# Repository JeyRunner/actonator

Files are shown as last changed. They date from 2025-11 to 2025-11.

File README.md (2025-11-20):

## Actonator - 3D Printable Robot Actuator


3D printable robot actuator with belt-driven gearbox and custom FOC driver board for the used BLDC motor.
It uses the [CAN SOT Protocol](https://github.com/JeyRunner/can-sot-protocol) for the communication, which allows to not only send commands and receive state changes but also to set configuration parameters dynamically during runtime.

### Features

- Driver board
  - Input: 10 - 24V
  - Output: can drive up to two BLDC motors, each output up to 10A
  - CAN bus communication
  - Encoders connected via two I2C connections
      - Alternatively via two SPI inputs
    - 12 bit encoders
- Gearbox
  - Fully 3d printable
  - 2 stage timing belt based reduction
  - Simple screw-based belt tensioning mechanism
  - ~1:20 reduction
  - Easily back drivable

### Project Structure
- `motor_driver/firmware`: C++ firmware code for the stm32 microcontroller
- `motor_driver/can_client_lib`: Contains the can bus communication protocol definition and host applications to configure and interface with the motor driver.
    - `motorControllerCanProtocol.def.yaml`: Contains the protocol definition.
- `motor_driver/hardware`: Kicad files with schematics for the board and PCB.
- `motor_driver/hardware/output`: Schematics, board layout and manufacturing files.
- `gearbox`: 3D printing stl files for the gearbox.

### Driver Board Electronics
This board is a dual channel brushless motor driver.
The design of the board can be found in the `hardware` subfolder.
In `hardware/output` are all generated files for all versions.

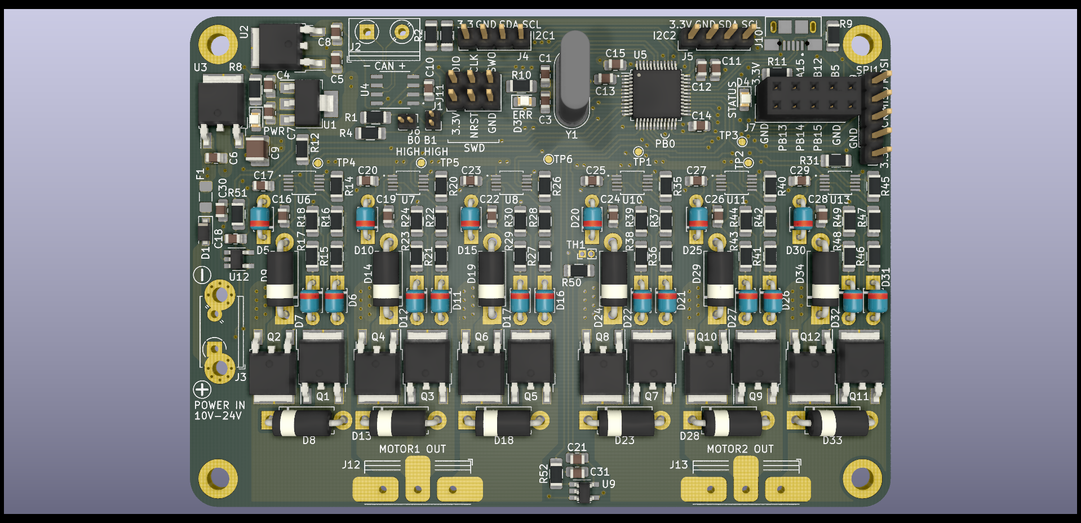
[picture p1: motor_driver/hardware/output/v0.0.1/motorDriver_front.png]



For the full schematic, see [hardware/motorDriver/output/v0.0.1/schematic.pdf](motor_driver/hardware/output/v0.0.1/schematic.pdf).

### Gearbox
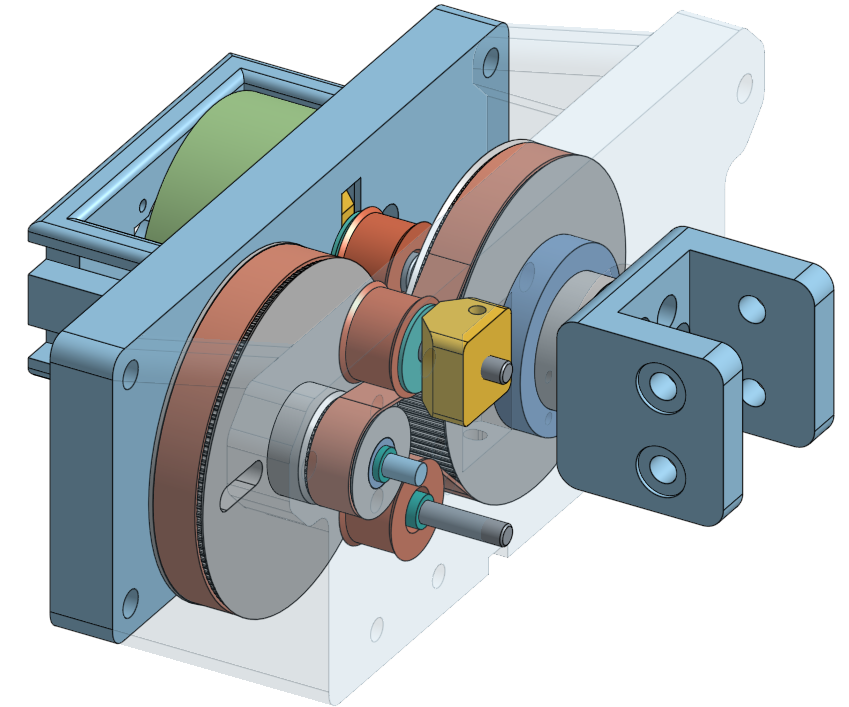
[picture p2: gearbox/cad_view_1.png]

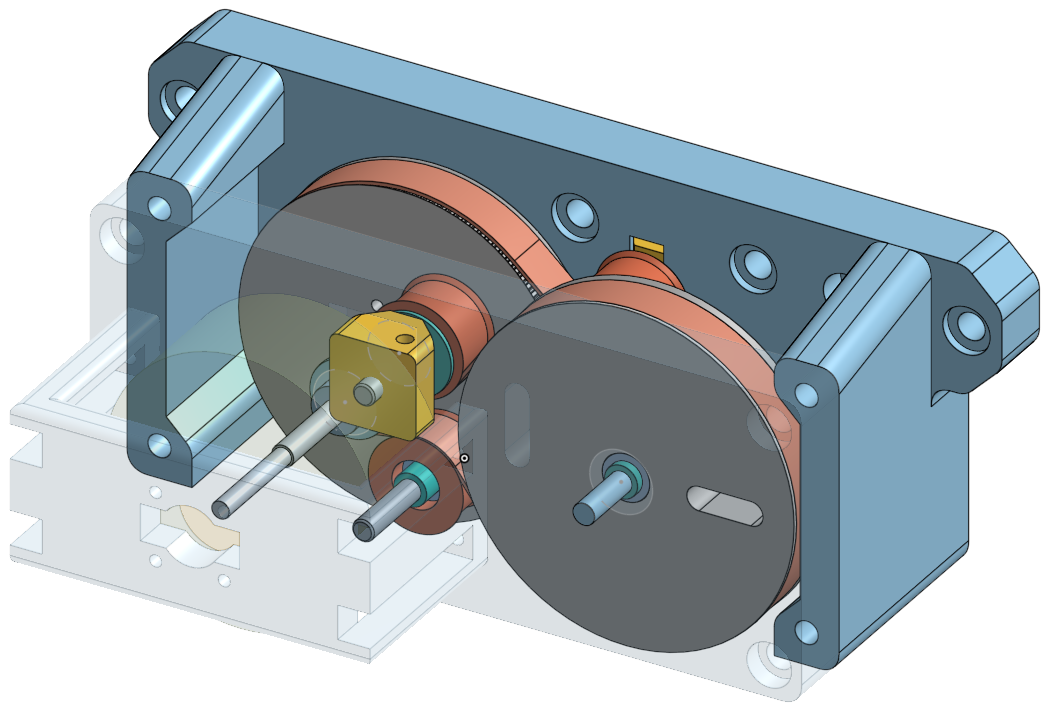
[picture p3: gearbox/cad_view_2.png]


### Usage
First look at [motor_driver/can_client_lib/README.md](motor_driver/can_client_lib/README.md) to compile the communication lib and host control application.
Then compile and flash the microcontroller firmware, see [motor_driver/firmware/README.md](motor_driver/firmware/README.md).

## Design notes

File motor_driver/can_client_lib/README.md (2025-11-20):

# MotorDriver Can Client Library
Interface with the MotorDriver from linux via the can bus. 
Here also the can protocol is defined.

## Usage
First connect a usb-to-CAN adapter of your choice to the computer and setup the can interface:
```bash
sudo ip link set can0 up type can bitrate 500000

# check interface
sudo ifconfig

# test send something
cansend can0 123#42ff4545
```

For `canable` adapters there is a helper script for this in `tools/setup_slcand_can.sh`.

### Configure the Board and Move the Motor
You can configure the motor driver with the `configuration_tool`:
```bash
# in the build folder
# set gains:
./configuration_tool --can-interface can0 --client-id 1 --set-gain-p 1.0 --set-gain-d 0.05
```

Move the actuator in a sinusodial motion:
```bash
# here we also can update the gains:
./example_app -i can0 --client-id 1 \
  --loop-delay-ms 2 `--pd-sin-lambda 0.4` \
  --throttle-limit 0.9 --pd-sin-amplitude 10000 \
  --gain-p -1.5 --gain-d -0.00 
```

## Compile
### Compile the example and configuration execuables
```bash
# install deps
apt-get install libasio-dev libboost-coroutine-dev libboost-dev

mkdir build
cd build
cmake ..
make genCanSotHeaders   # gen protocol headers first
make example_app 
make configuration_tool 
```

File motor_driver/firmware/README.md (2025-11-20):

## Firmware for the Motor Driver Board
Implements field oriented control.

### Structure
```bash
└── src
    ├── canSot           # can protocol (contains autogenerated code)
    ├── cubeMxGenerated  # auto generated code
    ├── motordriver      # main implementation of the bldc motor driver
    └── stm32_custom     # stm specific hardware interface implementation
```

### Compile and Flash Firmware
Note that you first have to generate the can protocol code, see [can_client_lib/README.md](../can_client_lib/README.md) (here run `genCanSotHeaders`). The compile the firmware:
```
mkdir build
cd build
cmake ..
make
```
This will produce the binary `motorDriver_stm32.elf`.

Now you can program the micorcontroller with a programmer that is conneced to the host computer:
```bash
# in the firmware/ folder
openocd -f stm32F103_Debug_self_start.cfg \
	-c "program motorDriver_stm32.elf verify reset exit"
```

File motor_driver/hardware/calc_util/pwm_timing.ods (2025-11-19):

MOSFET |  | Fall Time | Min Pulse Time | Cicle duration (8Bit Res) | Max Freq (8bit Res)
 | @ 5V | 2,00E-05 | 2E-05 | 0,0051 | 196,078431372549
 | @ 10V

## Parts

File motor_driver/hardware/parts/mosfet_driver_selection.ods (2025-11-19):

Name | Functions | Cost for 1 Unit | Link
DRV8305N | - 3 Gait Drivers for the 3 Phases (3 or 6 PWM) - 3 Current Sense Amps for all 3 Phases | ~ 5 EUR | https://www.lcsc.com/product-detail/Motor-Driver-ICs_Texas-Instruments-DRV8305NQPHPRQ1_C701780.html

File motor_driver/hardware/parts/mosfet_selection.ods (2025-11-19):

Calculation Formulas: |  | MOSFET |  |  |  |  |  | 10A |  | 20A |  | 30A
 |  |  | Pack | Vmax GateSource | Q Total (nC) | RDS(ON) | °C/Watt | Power (W) | Temp °C (Room = 20°C) | Power | Temp (Room = 20°C) | Power | Temp (Room = 20°C) | Cost (10 pieces, €)
Power: | RDS(ON) * (Current2) | IRFZ44N (Current) | tht |  | 63 | 0.0175 | 62 | 1.75 | 128.5 | 7 | 454 | 15.75 | 996.5
 |  | AP120N03K | smd big |  | 34 | 0.006 | 62.5 | 0.6 | 57.5 | 2.4 | 170 | 5.4 | 357.5 | 0.98
 |  | SE30100B | smd small |  | 70 | 0.004 | 75 | 0.4 | 50 | 1.6 | 140 | 3.6 | 290
 |  |  |  |  |  |  |  | 0 | 20 | 0 | 20 | 0 | 20
 |  | VSD004N03MS | smd big |  | 85 | 0.004 | 50 | 0.4 | 40 | 1.6 | 100 | 3.6 | 200 | 1.48 | https://www.lcsc.com/product-detail/MOSFETs_Vanguard-VSD004N03MS_C427022.html
 |  |  |  |  |  |  |  | 0 | 20 | 0 | 20 | 0 | 20
 |  | LNG03R031 | smd big |  | 146 | 0.0031 | 68 | 0.31 | 41.08 | 1.24 | 104.32 | 2.79 | 209.72 | 1.98 | https://www.lcsc.com/product-detail/MOSFETs_LONTEN-LNG03R031_C779904.html
 |  |  |  |  |  |  |  | 0 | 20 | 0 | 20 | 0 | 20
 |  | FHP100N03C | tht |  | 26 | 0.0048 | 62.5 | 0.48 | 50 | 1.92 | 140 | 4.32 | 290 | 1.87
 |  |  |  |  |  |  |  | 0 | 20 | 0 | 20 | 0 | 20
 |  |  |  |  |  |  |  | 0 | 20 | 0 | 20 | 0 | 20
 |  | HUAYI HYG030N03LQ1D | smd big |  |  | 0.003 | 110 | 0.3 | 53 | 1.2 | 152 | 2.7 | 317
 |  | TTD120N03AT | smd big |  | 89 | 0.0034 | 60 | 0.34 | 40.4 | 1.36 | 101.6 | 3.06 | 203.6 | 1.52 | https://www.lcsc.com/product-detail/MOSFETs_WUXI-UNIGROUP-MICRO-TTD120N03AT_C691675.html
 |  | HSU150N03 | smd big |  | 39 | 0.0032 | 62 | 0.32 | 39.84 | 1.28 | 99.36 | 2.88 | 198.56 | 2.27 | https://www.lcsc.com/product-detail/MOSFETs_HUASHUO-HSU150N03_C845614.html
 |  | YJG150N03A | smd small |  |  |  |  | 0 | 20 | 0 | 20 | 0 | 20
 |  |  |  |  |  |  |  | 0 | 20 | 0 | 20 | 0 | 20
 |  |  |  |  |  |  |  | 0 | 20 | 0 | 20 | 0 | 20
 |  | No avail | smd small |  | 41 | 0.0018 | 235 | 0.18 | 62.3 | 0.72 | 189.2 | 1.62 | 400.7
 |  |  |  |  |  |  |  | 0 | 20 | 0 | 20 | 0 | 20
 |  |  |  |  |  |  |  | 0 | 20 | 0 | 20 | 0 | 20
 |  | SiR150DP | smd small | 45 V | 32 | 0.0028 | 62.5 | 0.28 | 37.5 | 1.12 | 90 | 2.52 | 177.5 | 9.2 | https://www.mouser.de/ProductDetail/Vishay-Siliconix/SIR150DP-T1-RE3?qs=BJlw7L4Cy78ko2ZoY53%252BgQ%3D%3D
 |  | TPH2R306NH1 | smd small |  |  | 0.0023 | 156 | 0.23 | 55.88 | 0.92 | 163.52 | 2.07 | 342.92
 |  |  |  |  |  |  |  | 0 | 20 | 0 | 20 | 0 | 20
 |  | NTMFS5C430NL | smd small | 40 V | 82 | 0.0014 | 50 | 0.14 | 27 | 0.56 | 48 | 1.26 | 83 | 8 | https://www.lcsc.com/product-detail/MOSFETs_onsemi-NTMFS5C430NLT1G_C194661.html
 |  | From old Multiplex ESC NTMFS4833N | smd small | 30V | 58 | 0.002 | 117 | 0.2 | 43.4
 |  | Driver Current = 1.2A |  |  | T = Q / I

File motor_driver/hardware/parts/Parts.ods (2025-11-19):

Part(s) Type | Values | Parts Per Value | Package/ Dimensions | Required | Voltage | Notes | Picture | Cost With Shipping | Url
Resistor SMD Kit | 0 ohm, 1 Ohm, 2,2 Ohm, 3,3 Ohm, 4,7 Ohm, 5,1 Ohm, 10 ohm, 15 Ohm, 22 Ohm, 33 Ohm, 47 Ohm, 51 Ohm, 62 ohm, 82 Ohm, 100 Ohm, 120 Ohm, 150 Ohm, 180 Ohm, 200 ohm, 220 Ohm, 240 Ohm, 270 Ohm, 300 Ohm, 330 Ohm, 470 ohm, 510 Ohm, 560 Ohm, 680 Ohm, 820 Ohm, 1K Ohm, 1,2 K Ohm, 1,5 K Ohm, 1,8 K Ohm, 2K Ohm, 2,2 K Ohm, 3K Ohm, 3,3 K Ohm, 4,7 K Ohm, 5,1 K Ohm, 5,6 K Ohm, 7,5 K Ohm, 10K Ohm, 12K Ohm, 15K Ohm, 18K Ohm, 20K Ohm, 22K Ohm, 33K Ohm, 43K Ohm, 47K Ohm, 51K Ohm, 75K Ohm, 100K Ohm, 200K Ohm, 300K Ohm, 390K Ohm, 470K Ohm, 680K Ohm, 1M Ohm, 10M Ohm | 20 | Package Code: Imperial: 1206 Metric: 3216 | yes |  | ¼ Watt |  | 7.61 | https://de.aliexpress.com/item/1005003021538603.html?spm=a2g0s.8937460.0.0.38652e0eIeFj74
0805 SMD Ceramic Capacitor Kit |  | 25 | Package Code: Imperial: 0805 | yes |  |  |  | 8.79 | https://www.aliexpress.com/item/592923241.html?pdp_ext_f=%7B%22sku_id%22%3A%2257665256609%22%7D
SMD 0805 LED | Red Green Blue Yellow White | 20 | Package Code: Imperial: 0805 | yes |  |  |  | 2.88 | https://www.ebay.de/itm/373436218990?hash=item56f2887e6e:g:Zz8AAOSwRF1gCoNk
STM32F103C8T6 |  | 1 |  | yes |  |  |  | 9.24 | https://de.aliexpress.com/item/1005002502652952.html
CAN Driver TJA1050 |  | 5 | sop-8 |  |  |  |  | 7.16 | https://de.aliexpress.com/item/1005001716591215.html
UF4007 Ultra Fast Diode |  | 100 | tht |  |  |  |  | 2.64 | https://de.aliexpress.com/item/32854878050.html?pdp_ext_f=%7B%22sku_id%22%3A%2265279246474%22%7D
AMS1117 Spannung Regler Kit | 1,2 V 1,5 V 1,8 V 2,5 V 3,3 V 5V | 10 | smd | OPTIONAL | Vin max = 12V |  |  | 5.06 | https://de.aliexpress.com/item/4000931454820.html
LM2937-3,3 Spannungs Regler 3.3V 500mA |  | 10 | smd | OPTIONAL [selected] | Vin max = 26V Vin min = 5V |  |  | 4.08 | https://de.aliexpress.com/item/1005002503564346.html
UA78M33CDCYR Spannungs Regler 3.3V 500mA |  | 10 | smd | OPTIONAL | Vin max = 25V |  |  | 6.69 | https://de.aliexpress.com/item/1005002054754217.html
L78M05CDT Spannungs Regler 5V 500mA |  | 10 | smd | OPTIONAL | Vin max = 35V Vin min = 7V |  |  | 2.66 | https://de.aliexpress.com/item/32493217336.html
L78xx Spannungs Kit | Adjustable 5V 6V 8V 9V 10V 12V 15V 18V 24V LM317T L7805 L7806 L7808 L7809 L7810 L7812 L7815 L7818 L7824 | 10 | THT | OPTIONAL [selected] | [For Vout = 5V] Vin max = 35V Vin min = 7V |  |  | 7.72
Fuse | 0.5A | 10 | smd | OPTIONAL |  |  |  | 2.00 | https://www.aliexpress.com/item/32901034711.html?pdp_ext_f=%7B%22sku_id%22%3A%2266684643036%22%7D
 |  |  |  |  |  |  |  | SUM:
 |  |  |  |  |  |  |  | 28.52 €
LCSC PARTS
Part(s) Type | Values | Parts Per Value | Package/ Dimensions | Required | Voltage | Notes | Picture | Cost | Url
UF4007 Ultra Fast Diode |  | 100 | tht | yes |  |  |  | 1.34 | https://www.lcsc.com/product-detail/Diodes-Fast-Recovery-Rectifiers_SUNMATE-Elec-UF4007_C424496.html
CAN Driver TJA1050 |  | 5 | sop-8 | yes |  |  |  | 5.05 | https://www.lcsc.com/product-detail/CAN-ICs_NXP-Semicon-TJA1050T-CM-118_C6952.html
LM2937-3,3 Spannungs Regler 3.3V 500mA |  | 2 | smd | yes | Vin max = 26V Vin min = 5V |  |  | 0.78 | https://www.lcsc.com/product-detail/Linear-Voltage-Regulators-LDO_UTC-Unisonic-Tech-LM2937L-33-TQ2-R_C87307.html
UA78M33CDCYR Spannungs Regler 3.3V 500mA |  | 2 | SMD | yes | Vin max = 25V Vin min = 5V |  |  | 0.89
L78M05CDT Spannungs Regler 5V 500mA |  | 10 | smd | yes | Vin max = 35V Vin min = 7V |  |  | 1.14 | https://www.lcsc.com/product-detail/Linear-Voltage-Regulators-LDO_STMicroelectronics-L78M05CDT-TR_C55509.html
KIA78D09F-RTF/P Spannungs Regler 9V 1A |  | 5 | SMD | yes | Vin max = 35V Vin min = 9.5V |  |  | 0.80 € | https://www.lcsc.com/product-detail/Linear-Voltage-Regulators-LDO_KEC-Semicon-KIA78D09F-RTF-P_C69764.html
GRM32ER61C476KE15L Ceramic Capacitor 47uF 16V |  | 5 | smd | yes |  |  |  | 0.83 | https://www.lcsc.com/product-detail/Multilayer-Ceramic-Capacitors-MLCC-SMD-SMT_Murata-Electronics-GRM32ER61C476KE15L_C77101.html
Fuse 30A 24V |  | 5 | smd | yes |  | Breaking Capacity: 150A |  | 0.5 | https://www.lcsc.com/product-detail/Fuses_Shenzhen-JDT-Fuse-JFC1206-2300FS_C136359.html
Fuse 500mA 63V |  | 10 | smd | yes |  |  |  | 0.6
Micro USB B Connector |  | 20 | smd | yes |  |  |  | 0.44 | https://www.lcsc.com/product-detail/USB-Connectors_XKB-Connectivity-U254-051T-4BH83-F1S_C397452.html
Screw terminaL 3 PIN |  | 10 | tht | yes |  |  |  | 0.93 | https://www.lcsc.com/product-detail/Screw-terminal_Ningbo-Kangnex-Elec-WJ126V-5-0-3P_C8401.html
Screw terminaL 2 PIN |  | 5 |  |  |  |  |  | 0.31
LM5106MMX |  | 6 | smd | yes |  |  |  | 7.24
MOSFETS LNG03R031 |  |  |  | yes |  |  |  | 2.38
 |  |  |  |  |  |  | -- SHIPPING | 4.77
 |  |  |  |  |  |  |  | SUM:
 |  |  |  |  |  |  |  | 27.22 €

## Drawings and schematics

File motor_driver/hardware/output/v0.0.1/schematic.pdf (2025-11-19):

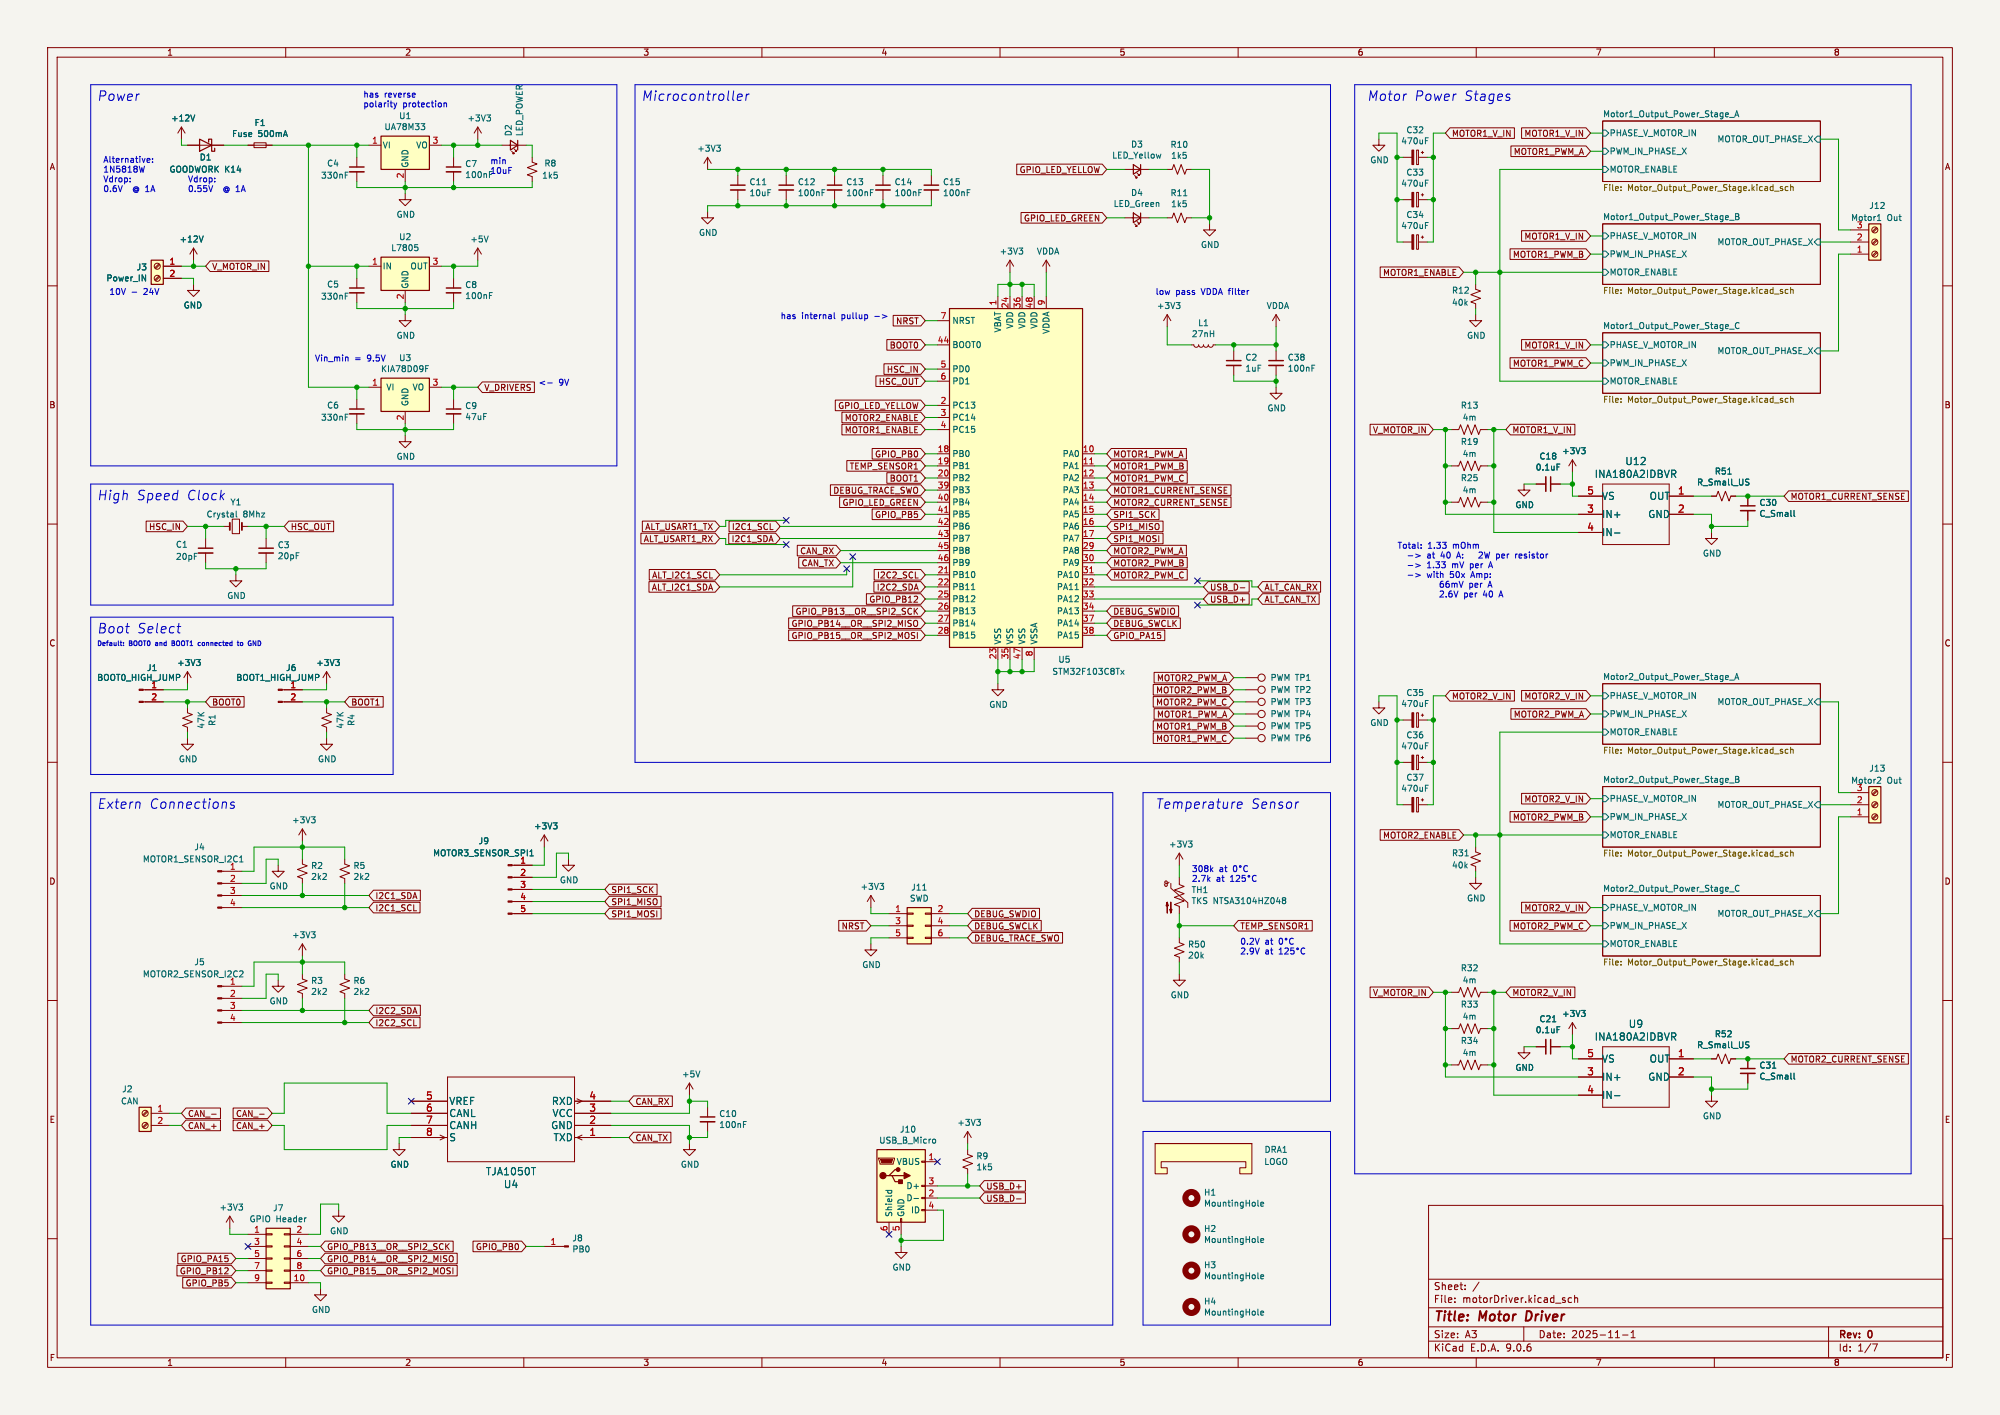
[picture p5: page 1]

2 VO 3 U1 UA78M33 GND GND GND

low pass VDDA filter

1 VSS 23 VDD 24 VSS 35 VDD 36 VSS 47 VDD 48 VSSA

Id: 1/7 Title: Motor Driver File: motorDriver.kicad_sch Sheet: /

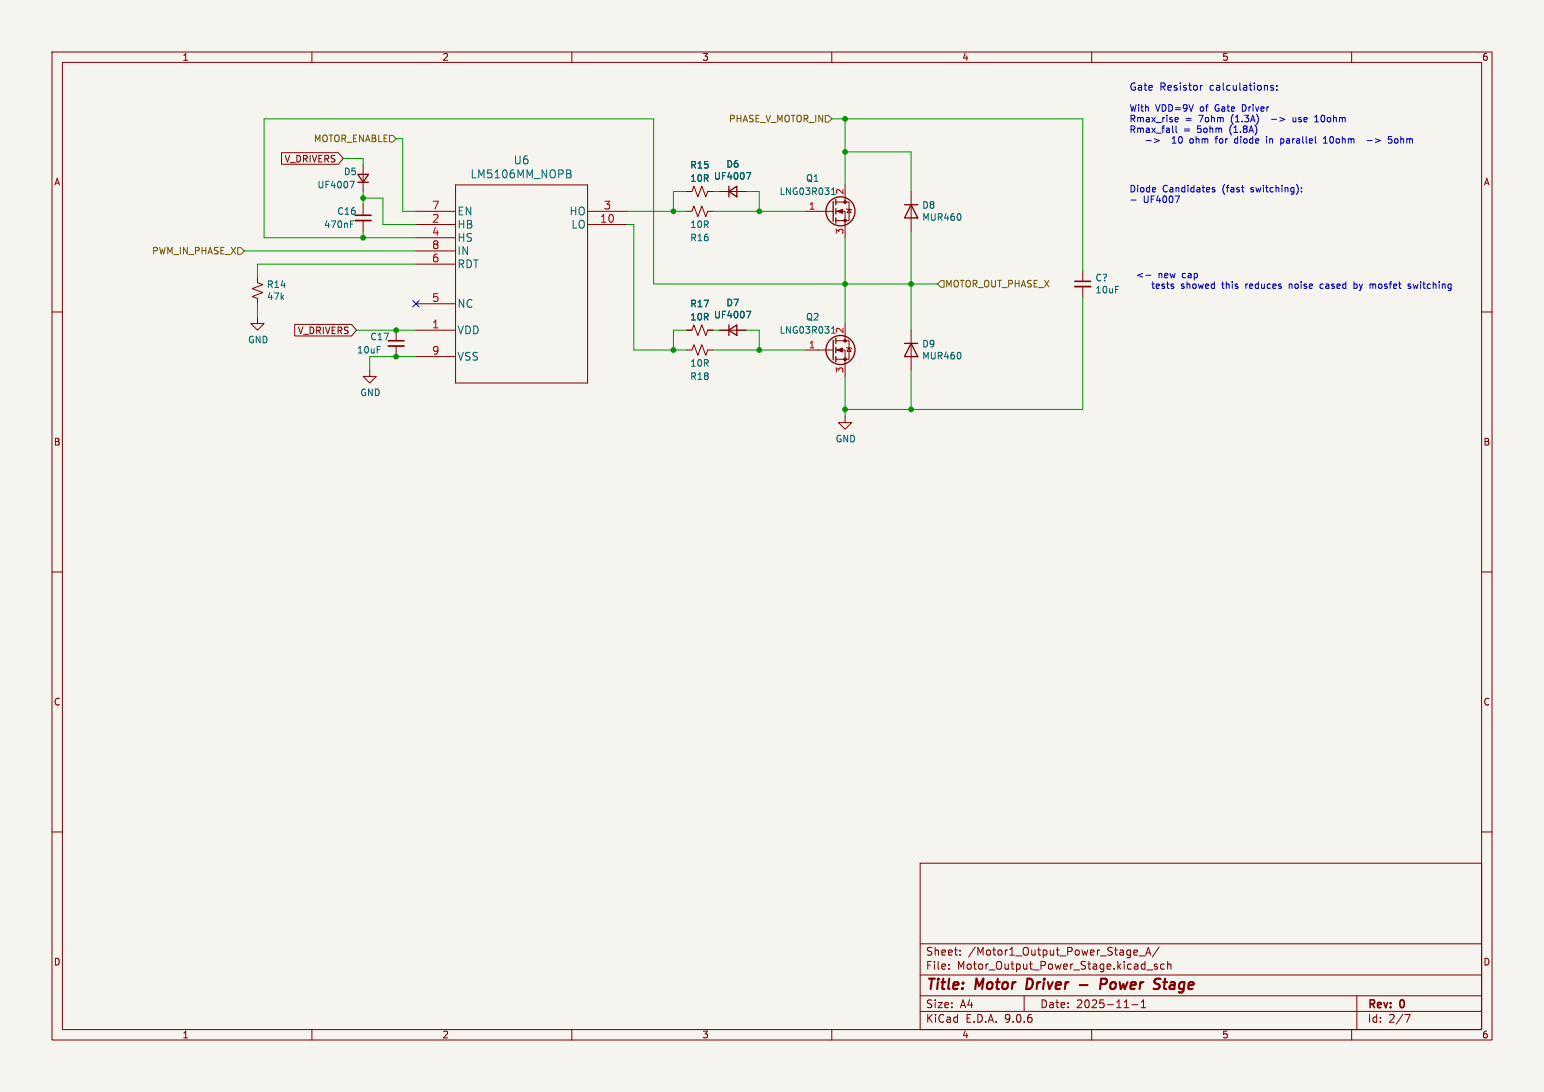
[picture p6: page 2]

File: Motor_Output_Power_Stage.kicad_sch Sheet: /Motor1_Output_Power_Stage_A/
Id: 2/7 Title: Motor Driver - Power Stage

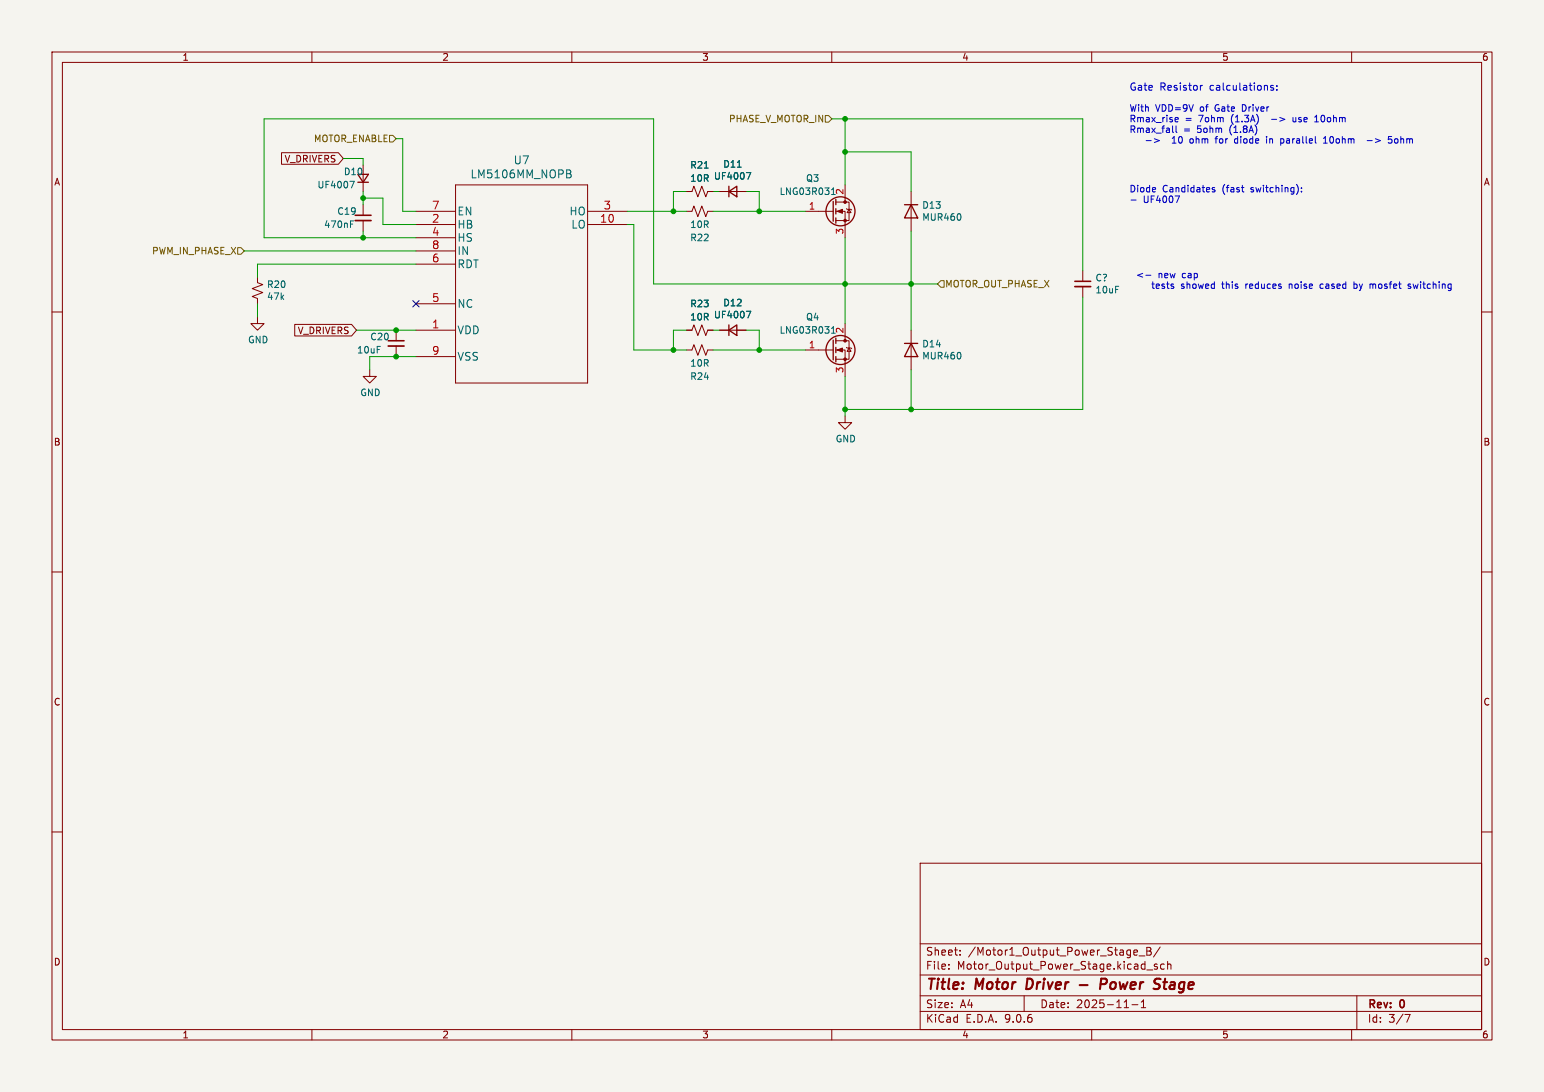
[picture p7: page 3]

File: Motor_Output_Power_Stage.kicad_sch Sheet: /Motor1_Output_Power_Stage_B/
Id: 3/7 Title: Motor Driver - Power Stage

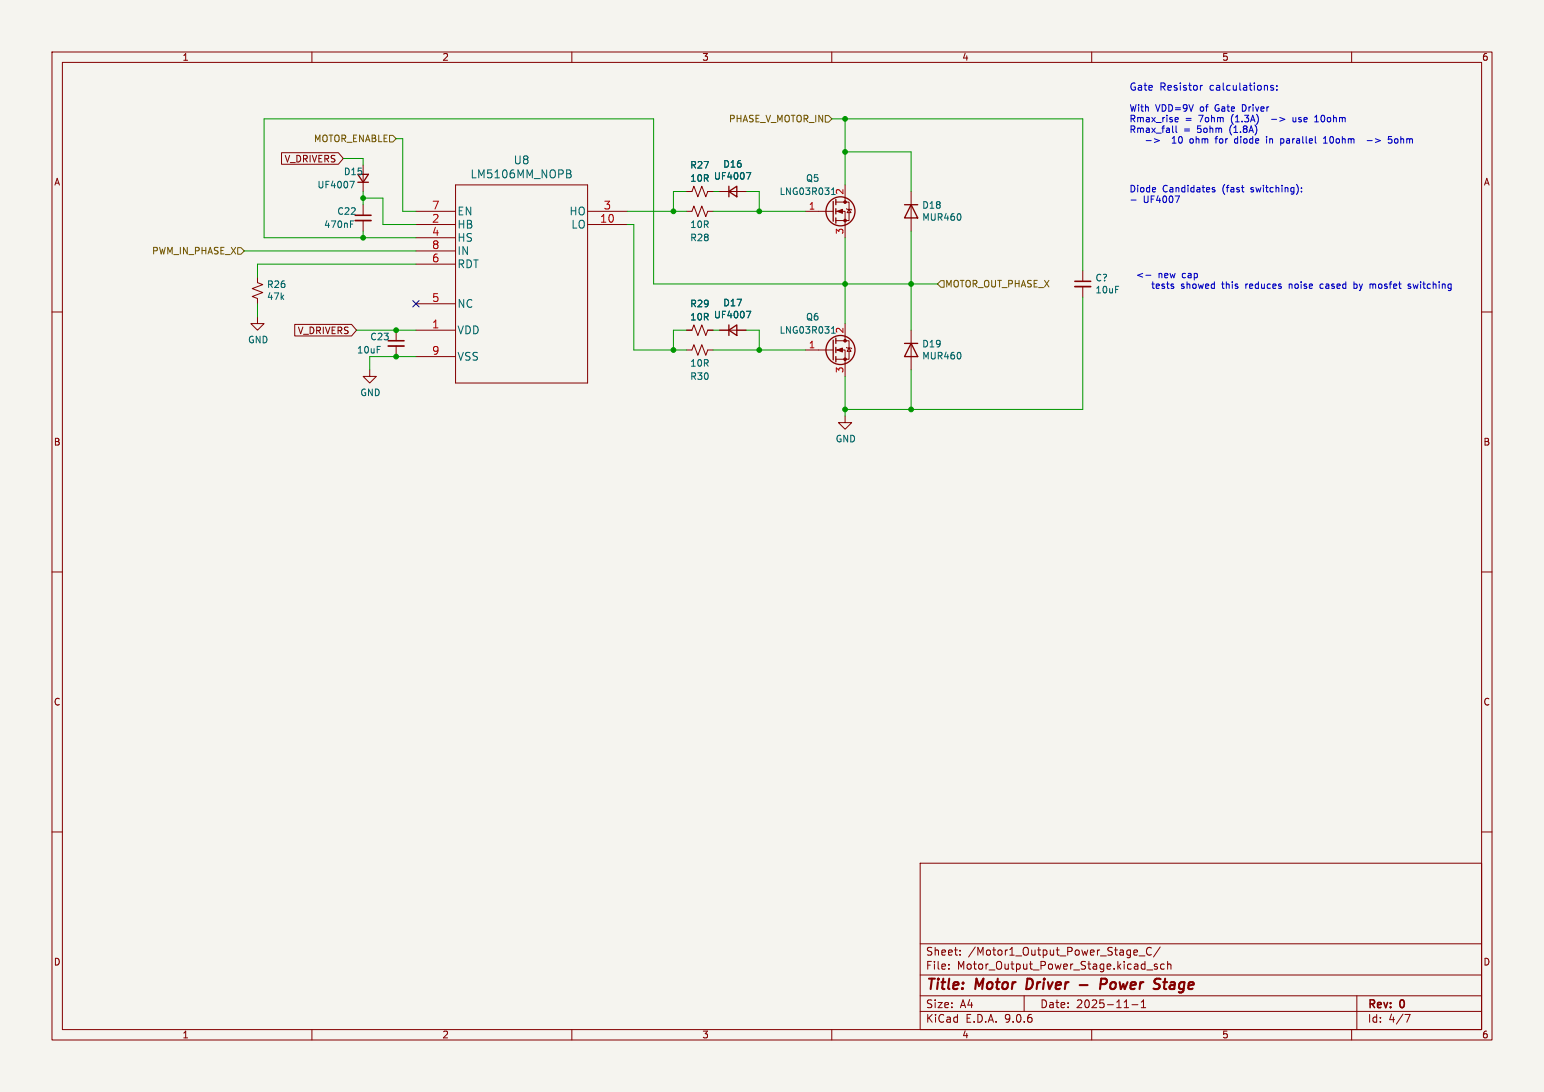
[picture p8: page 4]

File: Motor_Output_Power_Stage.kicad_sch Sheet: /Motor1_Output_Power_Stage_C/
Id: 4/7 Title: Motor Driver - Power Stage

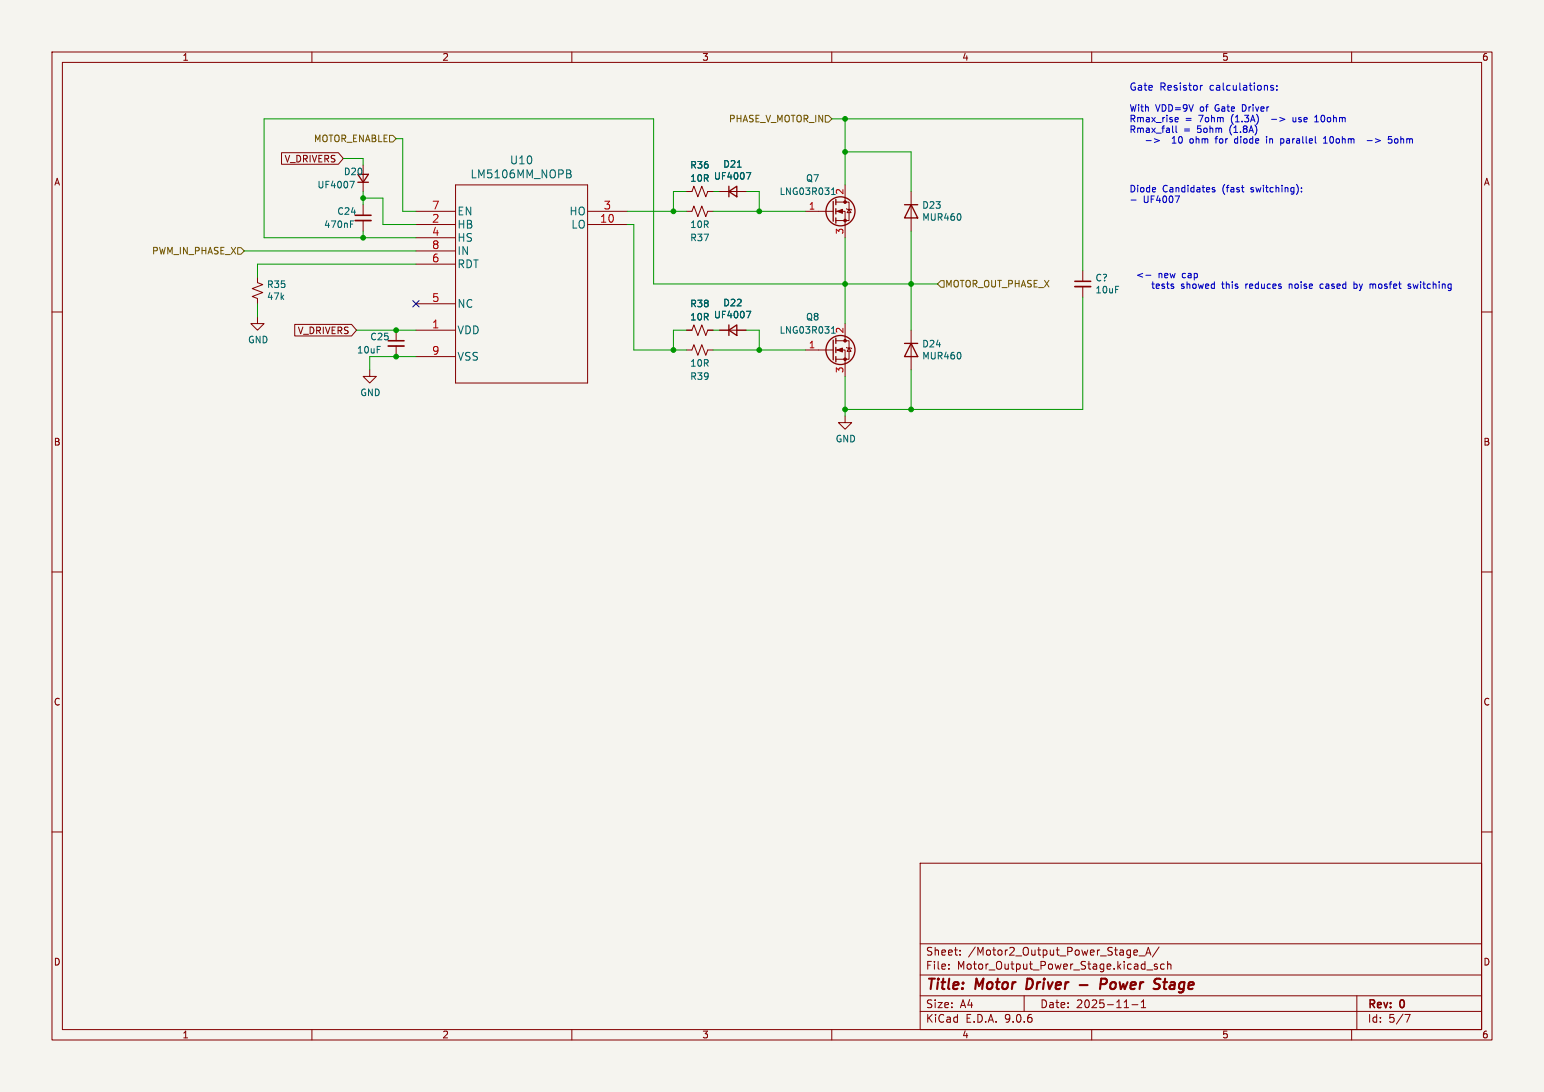
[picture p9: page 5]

File: Motor_Output_Power_Stage.kicad_sch Sheet: /Motor2_Output_Power_Stage_A/
Id: 5/7 Title: Motor Driver - Power Stage

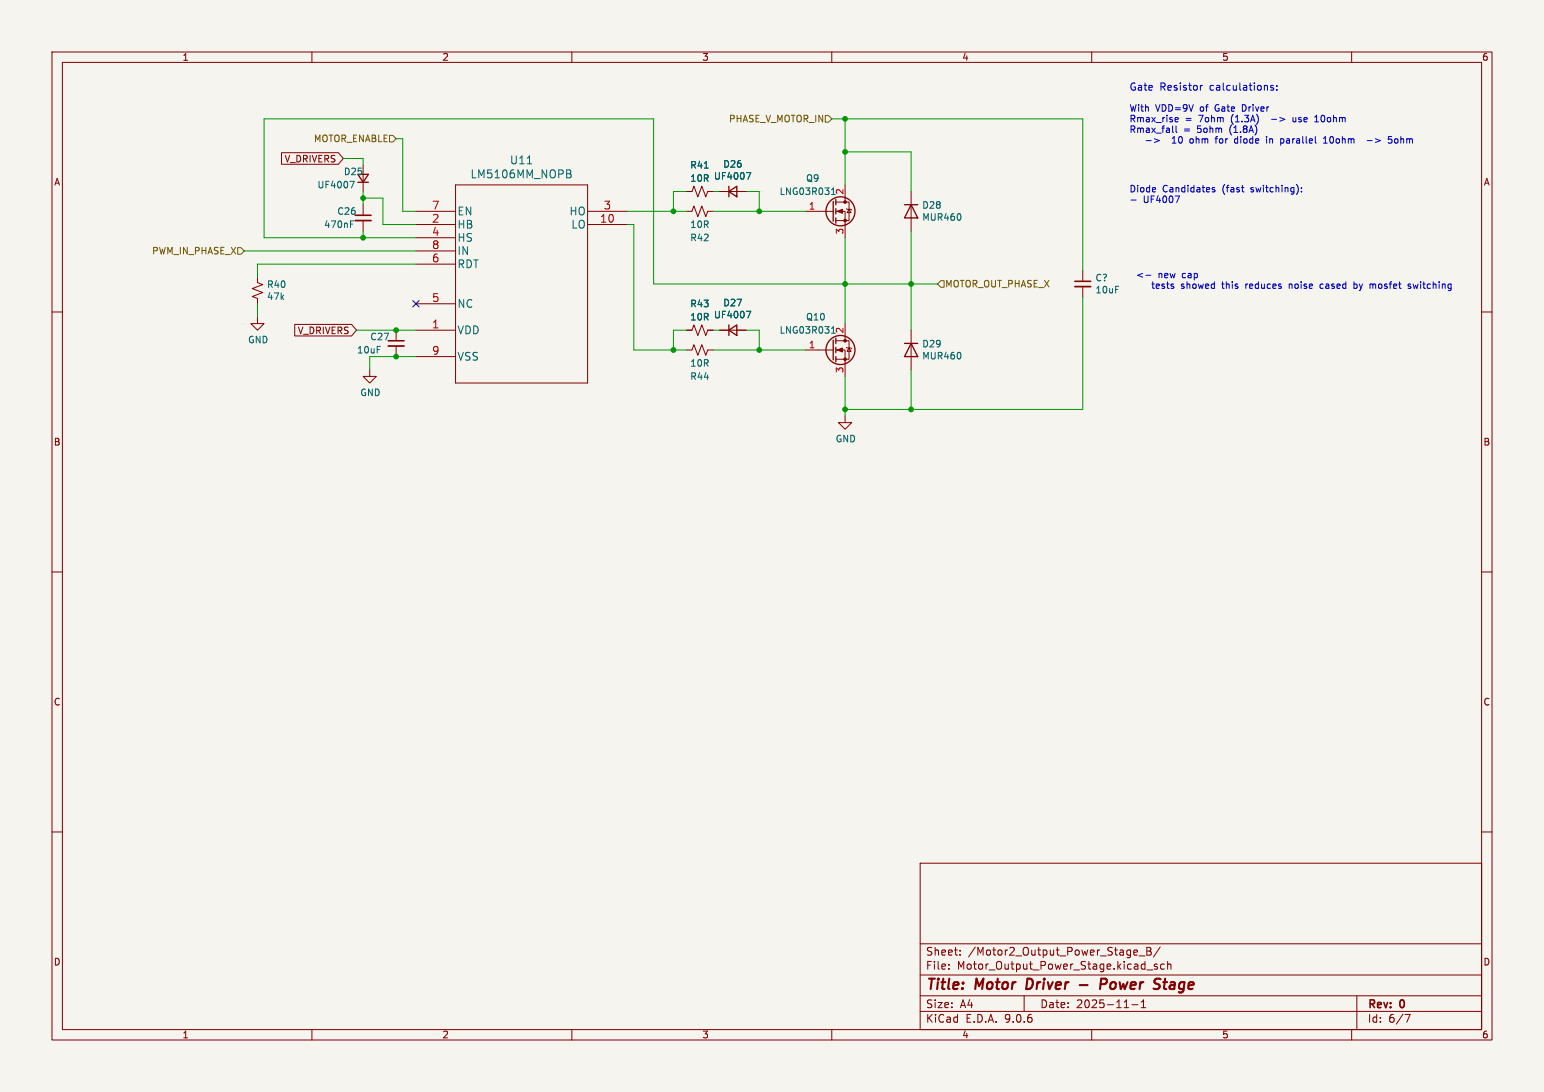
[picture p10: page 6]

File: Motor_Output_Power_Stage.kicad_sch Sheet: /Motor2_Output_Power_Stage_B/
Id: 6/7 Title: Motor Driver - Power Stage

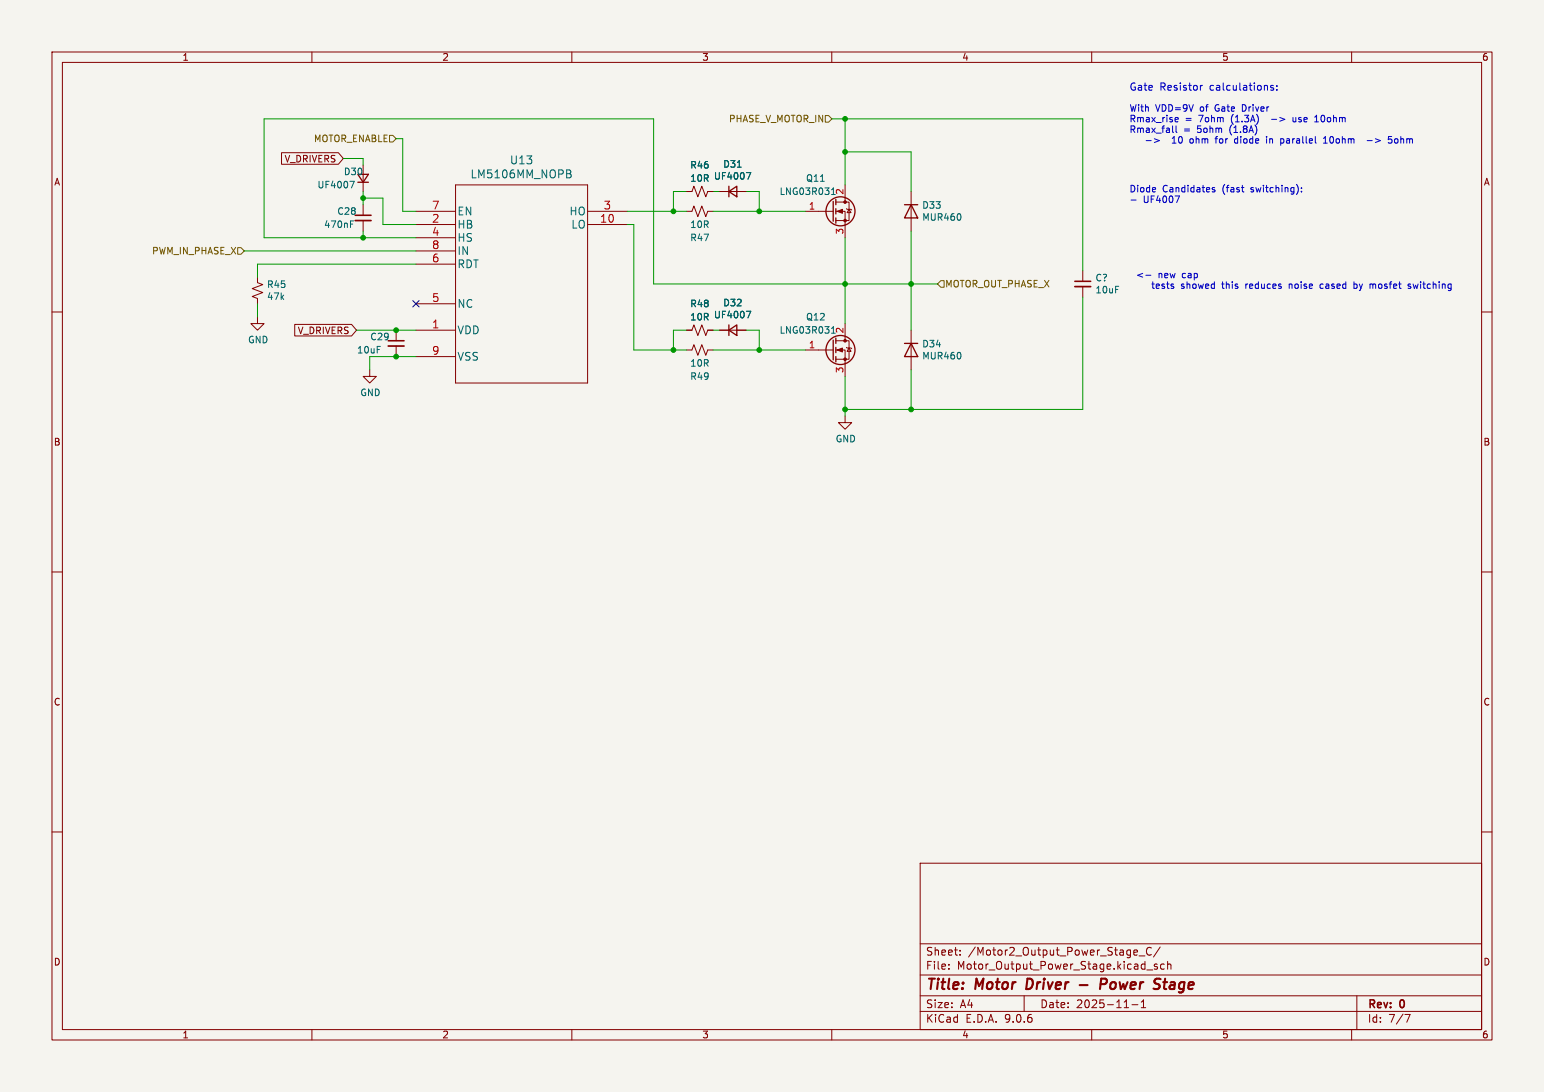
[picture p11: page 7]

File: Motor_Output_Power_Stage.kicad_sch Sheet: /Motor2_Output_Power_Stage_C/
Id: 7/7 Title: Motor Driver - Power Stage

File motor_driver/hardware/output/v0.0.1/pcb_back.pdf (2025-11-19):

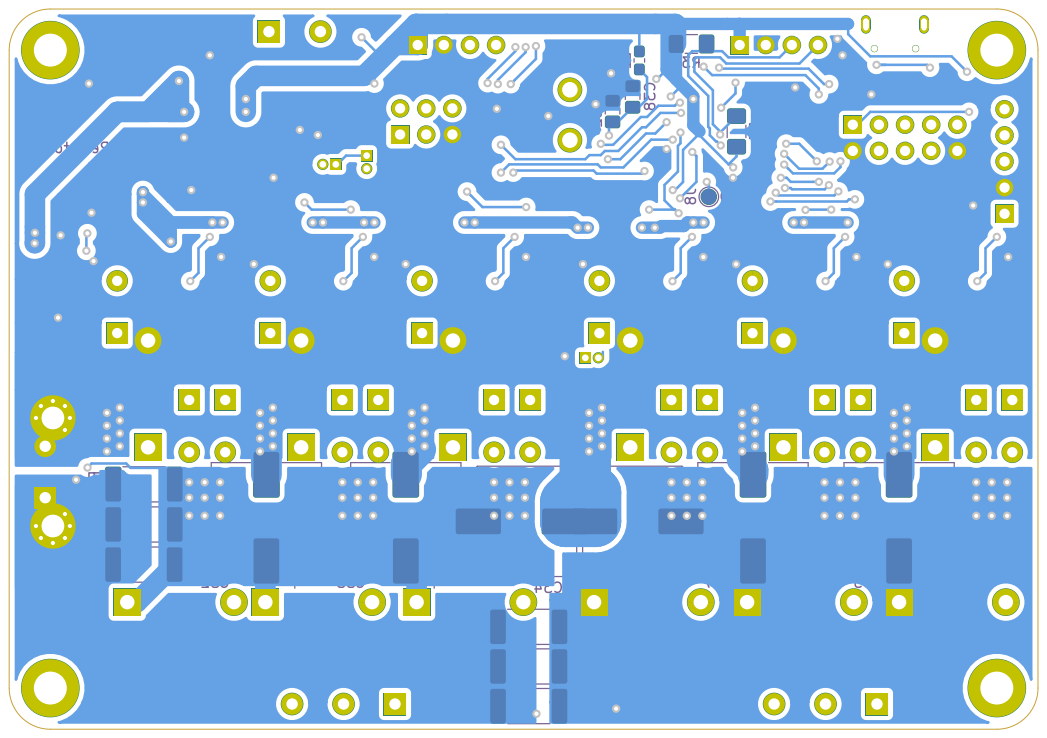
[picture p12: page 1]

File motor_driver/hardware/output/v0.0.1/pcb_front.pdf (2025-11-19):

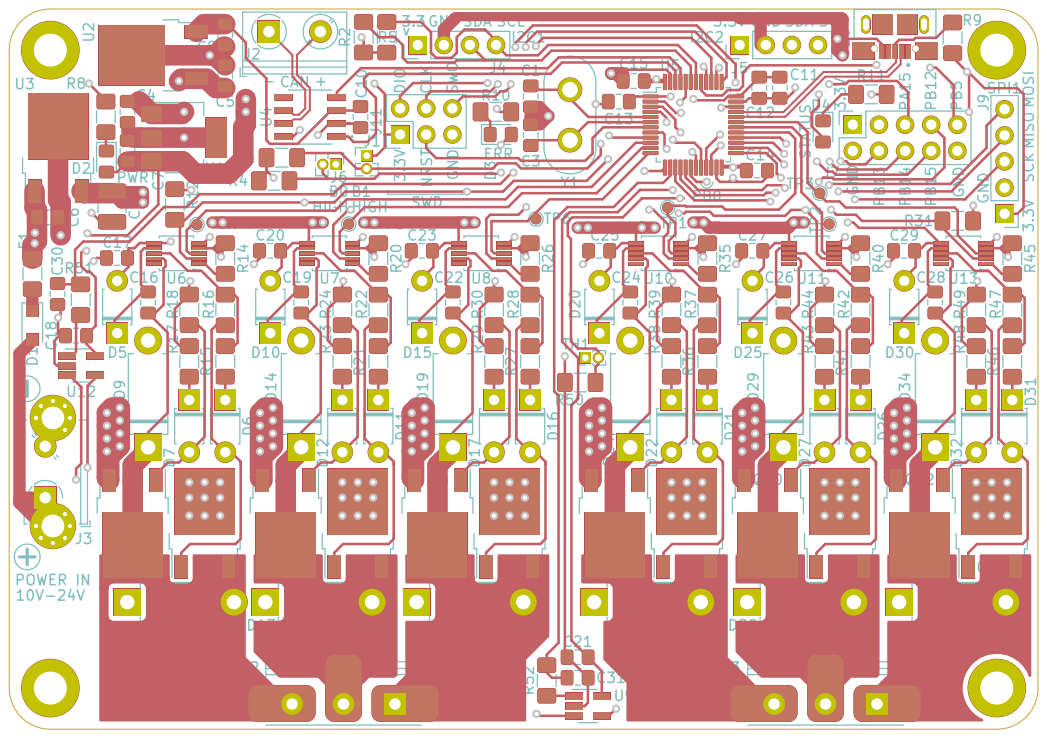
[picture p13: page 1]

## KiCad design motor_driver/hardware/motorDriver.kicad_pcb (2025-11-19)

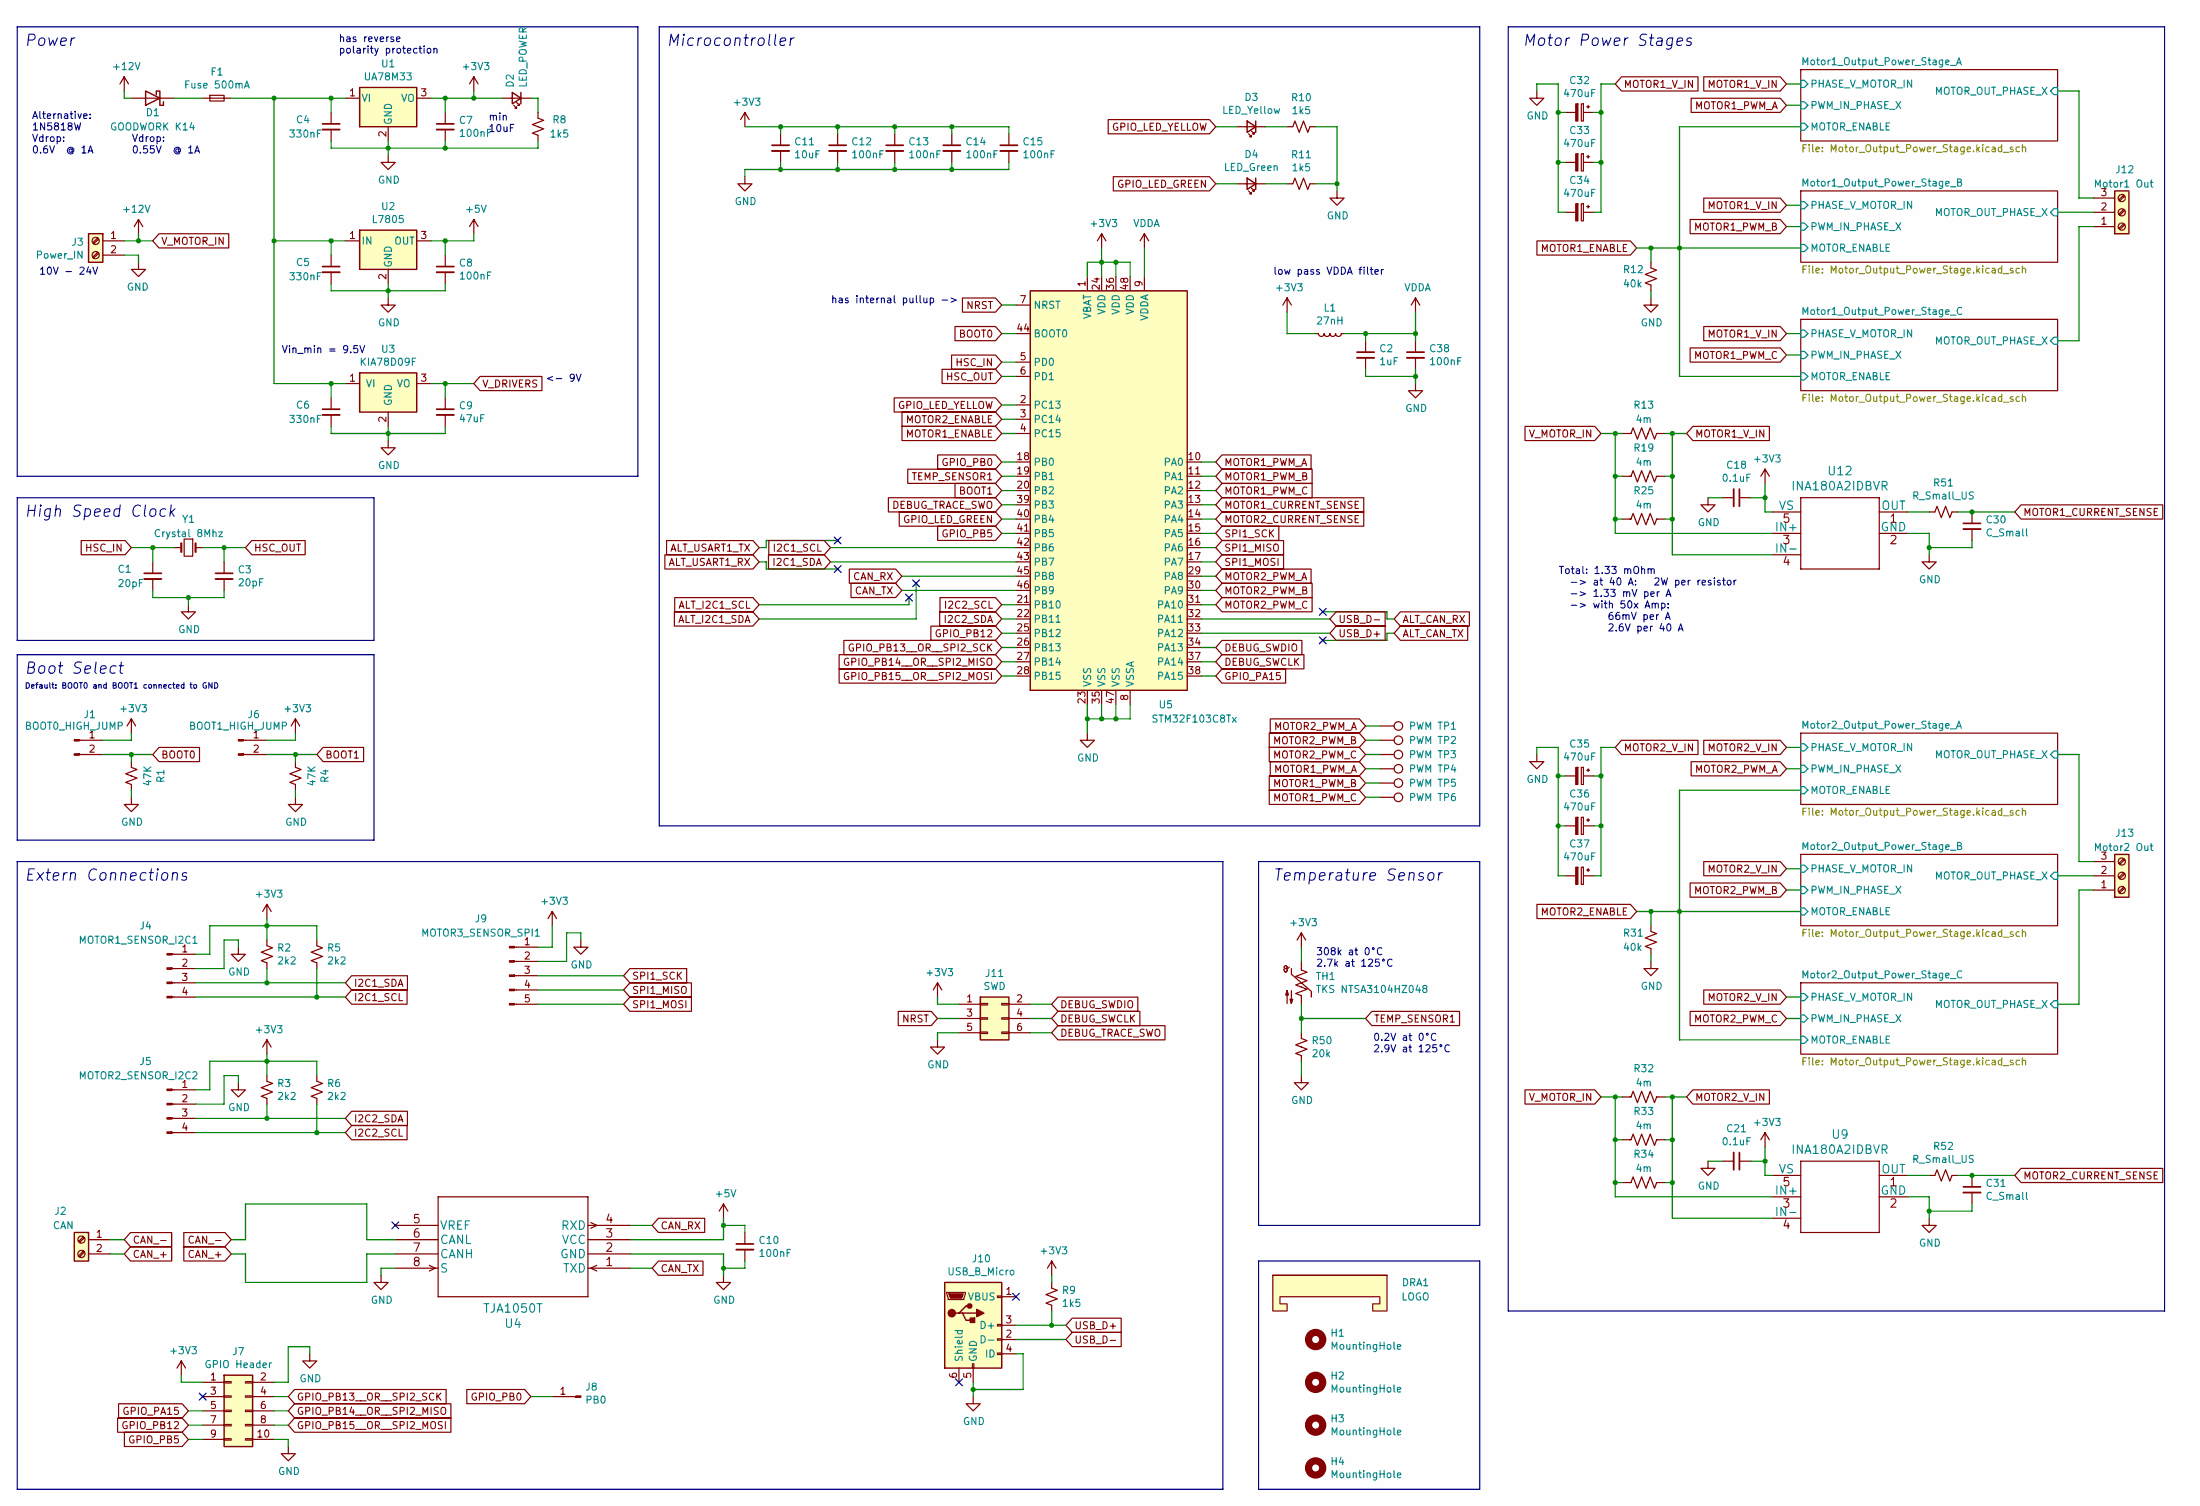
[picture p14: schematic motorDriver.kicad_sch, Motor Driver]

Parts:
C1, C3: 20pF; C_0805_2012Metric_Pad1.15x1.40mm_HandSolder
C2: 1uF; C_0805_2012Metric_Pad1.15x1.40mm_HandSolder
C4, C5, C6: 330nF; C_0805_2012Metric_Pad1.15x1.40mm_HandSolder
C7, C8, C10, C12, C13, C14, C15, C38: 100nF; C_0805_2012Metric_Pad1.15x1.40mm_HandSolder
C9: 47uF; C_1210_3225Metric_Pad1.42x2.65mm_HandSolder
C11: 10uF; C_0805_2012Metric_Pad1.15x1.40mm_HandSolder
C18, C21: 0.1uF; C_0805_2012Metric_Pad1.15x1.40mm_HandSolder
C30, C31: C_Small; C_0805_2012Metric_Pad1.15x1.40mm_HandSolder
C32, C33, C34, C35, C36, C37: 470uF; CP_Elec_10x10.5
D1: GOODWORK K14; D_SOD-123F
D2: LED_POWER; LED_0805_2012Metric_Pad1.15x1.40mm_HandSolder
D3: LED_Yellow; LED_0805_2012Metric_Pad1.15x1.40mm_HandSolder
D4: LED_Green; LED_0805_2012Metric_Pad1.15x1.40mm_HandSolder
DRA1: LOGO; logo
F1: Fuse 500mA; Fuse_1206_3216Metric_Pad1.42x1.75mm_HandSolder
H1, H2, H3, H4: MountingHole; MountingHole_3.2mm_M3_DIN965_Pad
J1: BOOT0_HIGH_JUMP; PinHeader_1x02_P1.27mm_Vertical__smallerOutline
J2: CAN; TerminalBlock_RND_205-00045_1x02_P5.00mm_Horizontal
J3: Power_IN; TerminalBlock_RND_205-00045_1x02_P5.00mm_Horizontal___with_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
J4: MOTOR1_SENSOR_I2C1; PinHeader_1x04_P2.54mm_Vertical
J5: MOTOR2_SENSOR_I2C2; PinHeader_1x04_P2.54mm_Vertical
J6: BOOT1_HIGH_JUMP; PinHeader_1x02_P1.27mm_Vertical__smallerOutline
J7: GPIO Header; PinSocket_2x05_P2.54mm_Vertical
J8: PB0; TestPoint_Pad_D1.5mm
J9: MOTOR3_SENSOR_SPI1; PinHeader_1x05_P2.54mm_Vertical
J10: USB_B_Micro; XKB_U254-051T-4BH83-F1S
J11: SWD; PinHeader_2x03_P2.54mm_Vertical
J12: Motor1 Out; TerminalBlock_RND_205-00046_1x03_P5.00mm_Horizontal__extend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
J13: Motor2 Out; TerminalBlock_RND_205-00046_1x03_P5.00mm_Horizontal__extend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
L1: 27nH; L_0603_1608Metric_Pad1.05x0.95mm_HandSolder
R1, R4: 47K; R_1206_3216Metric_Pad1.42x1.75mm_HandSolder
R2, R3, R5, R6: 2k2; R_1206_3216Metric_Pad1.42x1.75mm_HandSolder
R8, R9, R10, R11: 1k5; R_1206_3216Metric_Pad1.42x1.75mm_HandSolder
R12, R31: 40k; R_1206_3216Metric_Pad1.42x1.75mm_HandSolder
R13, R19, R25, R32, R33, R34: 4m; R_2512_6332Metric_Pad1.52x3.35mm_HandSolder
R50: 20k; R_1206_3216Metric_Pad1.42x1.75mm_HandSolder
R51, R52: R_Small_US; R_1206_3216Metric_Pad1.42x1.75mm_HandSolder
TH1: TKS NTSA3104HZ048; TH_2PIN_1.27mm
TP1, TP2, TP3, TP4, TP5, TP6: PWM; TestPoint_Pad_D1.0mm
U1: UA78M33; SOT-223-3_TabPin2
U2: L7805; TO-252-2
U3: KIA78D09F; TO-252-2
U4: TJA1050T
U5: STM32F103C8Tx; LQFP-48_7x7mm_P0.5mm
U9, U12: INA180A2IDBVR; SOT-23-5_HandSoldering
Y1: Crystal 8Mhz; Crystal_HC50_Vertical

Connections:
+3V3: C7.1, C11.1, C12.1, C13.1, C14.1, C15.1, C18.1, C21.1, D2.2 (A), J1.1, J4.1, J5.1, J6.1, J7.1, J9.1, J11.1, L1.2, R2.1, R3.1, R5.1, R6.1, R9.1, TH1.1, U1.3 (VO), U5.1 (VBAT), U5.24 (VDD), U5.36 (VDD), U5.48 (VDD), U9.5 (VS), U12.5 (VS)
+5V: C8.1, C10.1, U2.3 (OUT), U4.3 (VCC)
/Motor1_Output_Power_Stage_A/MOTOR_OUT_PHASE_X: J12.3; also elsewhere on the board
/Motor1_Output_Power_Stage_B/MOTOR_OUT_PHASE_X: J12.2; also elsewhere on the board
/Motor1_Output_Power_Stage_C/MOTOR_OUT_PHASE_X: J12.1; also elsewhere on the board
/Motor2_Output_Power_Stage_A/MOTOR_OUT_PHASE_X: J13.3; also elsewhere on the board
/Motor2_Output_Power_Stage_B/MOTOR_OUT_PHASE_X: J13.2; also elsewhere on the board
/Motor2_Output_Power_Stage_C/MOTOR_OUT_PHASE_X: J13.1; also elsewhere on the board
BOOT0: J1.2, R1.2, U5.44 (BOOT0)
BOOT1: J6.2, R4.2, U5.20 (PB2)
CAN_+: J2.2, U4.7 (CANH)
CAN_-: J2.1, U4.6 (CANL)
CAN_RX: U4.4 (RXD), U5.45 (PB8)
CAN_TX: U4.1 (TXD), U5.46 (PB9)
DEBUG_SWCLK: J11.4, U5.37 (PA14)
DEBUG_SWDIO: J11.2, U5.34 (PA13)
DEBUG_TRACE_SWO: J11.6, U5.39 (PB3)
GND: C1.2, C2.2, C3.2, C4.2, C5.2, C6.2, C7.2, C8.2, C9.2, C10.2, C11.2, C12.2, C13.2, C14.2, C15.2, C18.2, C21.2, C30.2, C31.2, C32.2, C33.2, C34.2, C35.2, C36.2, C37.2, C38.2, J3.2, J4.2, J5.2, J7.2, J7.10, J9.2, J10.4 (ID), J10.5 (GND), J11.5, R1.1, R4.1, R8.1, R10.2, R11.2, R12.2, R31.2, R50.2, U1.2 (GND), U2.2 (GND), U3.2 (GND), U4.2 (GND), U4.8 (S), U5.8 (VSSA), U5.23 (VSS), U5.35 (VSS), U5.47 (VSS), U9.2 (GND), U12.2 (GND); also elsewhere on the board
GPIO_LED_GREEN: D4.2 (A), U5.40 (PB4)
GPIO_LED_YELLOW: D3.2 (A), U5.2 (PC13)
GPIO_PA15: J7.5, U5.38 (PA15)
GPIO_PB0: J8.1, U5.18 (PB0)
GPIO_PB5: J7.9, U5.41 (PB5)
GPIO_PB12: J7.7, U5.25 (PB12)
GPIO_PB13__OR__SPI2_SCK: J7.4, U5.26 (PB13)
GPIO_PB14__OR__SPI2_MISO: J7.6, U5.27 (PB14)
GPIO_PB15__OR__SPI2_MOSI: J7.8, U5.28 (PB15)
HSC_IN: C1.1, U5.5 (PD0), Y1.2
HSC_OUT: C3.1, U5.6 (PD1), Y1.1
I2C1_SCL: J4.4, R5.2, U5.42 (PB6)
I2C1_SDA: J4.3, R2.2, U5.43 (PB7)
I2C2_SCL: J5.4, R6.2, U5.21 (PB10)
I2C2_SDA: J5.3, R3.2, U5.22 (PB11)
MOTOR1_CURRENT_SENSE: C30.1, R51.1, U5.13 (PA3)
MOTOR1_ENABLE: R12.1, U5.4 (PC15); also elsewhere on the board
MOTOR1_PWM_A: TP4.1, U5.10 (PA0); also elsewhere on the board
MOTOR1_PWM_B: TP5.1, U5.11 (PA1); also elsewhere on the board
MOTOR1_PWM_C: TP6.1, U5.12 (PA2); also elsewhere on the board
MOTOR1_V_IN: C32.1, C33.1, C34.1, R13.1, R19.1, R25.1, U12.4 (IN-); also elsewhere on the board
MOTOR2_CURRENT_SENSE: C31.1, R52.1, U5.14 (PA4)
MOTOR2_ENABLE: R31.1, U5.3 (PC14); also elsewhere on the board
MOTOR2_PWM_A: TP1.1, U5.29 (PA8); also elsewhere on the board
MOTOR2_PWM_B: TP2.1, U5.30 (PA9); also elsewhere on the board
MOTOR2_PWM_C: TP3.1, U5.31 (PA10); also elsewhere on the board
MOTOR2_V_IN: C35.1, C36.1, C37.1, R32.1, R33.1, R34.1, U9.4 (IN-); also elsewhere on the board
NRST: J11.3, U5.7 (NRST)
unnamed: C4.1, C5.1, C6.1, F1.2, U1.1 (VI), U2.1 (IN), U3.1 (VI)
unnamed: D1.1 (K), F1.1
unnamed: D2.1 (K), R8.2
unnamed: D3.1 (K), R10.1
unnamed: D4.1 (K), R11.1
unnamed: R51.2, U12.1 (OUT)
unnamed: R52.2, U9.1 (OUT)
SPI1_MISO: J9.4, U5.16 (PA6)
SPI1_MOSI: J9.5, U5.17 (PA7)
SPI1_SCK: J9.3, U5.15 (PA5)
TEMP_SENSOR1: R50.1, TH1.2, U5.19 (PB1)
USB_D+: J10.3 (D+), R9.2, U5.33 (PA12)
USB_D-: J10.2 (D-), U5.32 (PA11)
VDDA: C2.1, C38.1, L1.1, U5.9 (VDDA)
V_DRIVERS: C9.1, U3.3 (VO); also elsewhere on the board
V_MOTOR_IN: D1.2 (A), J3.1, R13.2, R19.2, R25.2, R32.2, R33.2, R34.2, U9.3 (IN+), U12.3 (IN+)

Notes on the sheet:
Vdrop: 0.55V @ 1A
Default: BOOT0 and BOOT1 connected to GND
308k at 0°C 2.7k at 125°C
0.2V at 0°C 2.9V at 125°C
has reverse polarity protection
Vin_min = 9.5V
Extern Connections
Alternative: 1N5818W Vdrop: 0.6V @ 1A
Boot Select
10V - 24V
Temperature Sensor
Power
Microcontroller
Total: 1.33 mOhm -> at 40 A: ~{} 2W per resistor -> 1.33 mV per A -> with 50x Amp: 66mV per A 2.6V per 40 A
min 10uF
High Speed Clock
Motor Power Stages
low pass VDDA filter
<- 9V
has internal pullup ->

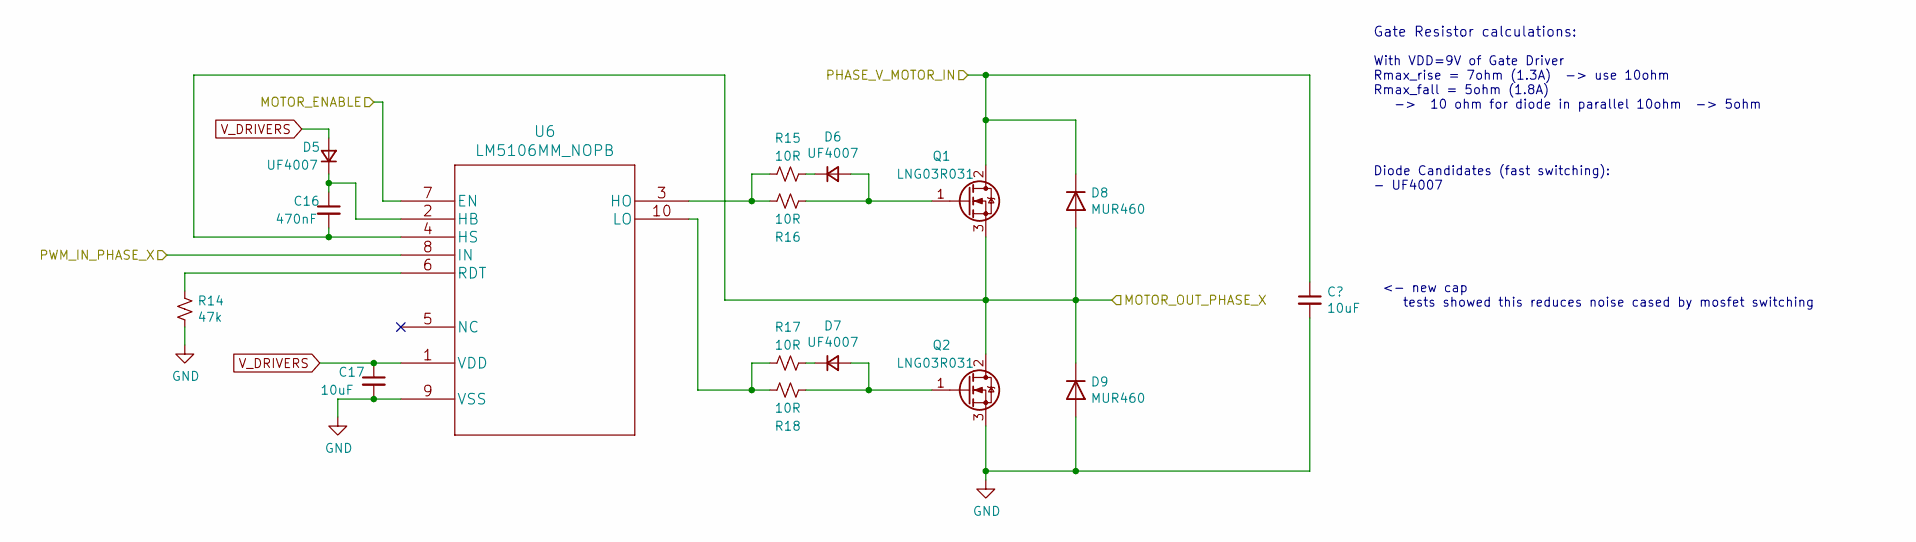
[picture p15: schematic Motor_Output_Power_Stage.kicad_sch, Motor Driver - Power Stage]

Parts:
C16: 470nF; C_0805_2012Metric_Pad1.15x1.40mm_HandSolder
C17: 10uF; C_0805_2012Metric_Pad1.15x1.40mm_HandSolder
D5, D6, D7: UF4007; D_T-1_P5.08mm_Horizontal
D8, D9: MUR460; D_DO-15_P10.16mm__H1.4mm_Horizontal
Q1, Q2: LNG03R031; TO-252-2
R14: 47k; R_1206_3216Metric_Pad1.42x1.75mm_HandSolder
R15, R16, R17, R18: 10R; R_1206_3216Metric_Pad1.42x1.75mm_HandSolder
U6: LM5106MM_NOPB; LM5106MM_slash_NOPB

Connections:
/Motor1_Output_Power_Stage_A/MOTOR_OUT_PHASE_X: C16.2, D8.2 (A), D9.1 (K), Q1.3 (S), Q2.2 (D), U6.4 (HS); also elsewhere on the board
GND: C17.2, D9.2 (A), Q2.3 (S), R14.2, U6.9 (VSS); also elsewhere on the board
MOTOR1_ENABLE: U6.7 (EN); also elsewhere on the board
MOTOR1_PWM_A: U6.8 (IN); also elsewhere on the board
MOTOR1_V_IN: D8.1 (K), Q1.2 (D); also elsewhere on the board
unnamed: C16.1, D5.1 (K), U6.2 (HB)
unnamed: D6.1 (K), R15.1
unnamed: D6.2 (A), Q1.1 (G), R16.1
unnamed: D7.1 (K), R17.1
unnamed: D7.2 (A), Q2.1 (G), R18.1
unnamed: R14.1, U6.6 (RDT)
unnamed: R15.2, R16.2, U6.3 (HO)
unnamed: R17.2, R18.2, U6.10 (LO)
V_DRIVERS: C17.1, D5.2 (A), U6.1 (VDD); also elsewhere on the board

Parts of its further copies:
C19, C22, C24, C26, C28: 470nF; C_0805_2012Metric_Pad1.15x1.40mm_HandSolder
C20, C23, C25, C27, C29: 10uF; C_0805_2012Metric_Pad1.15x1.40mm_HandSolder
D10, D11, D12, D15, D16, D17, D20, D21, D22, D25, D26, D27, D30, D31, D32: UF4007; D_T-1_P5.08mm_Horizontal
D13, D14, D18, D19, D23, D24, D28, D29, D33, D34: MUR460; D_DO-15_P10.16mm__H1.4mm_Horizontal
Q3, Q4, Q5, Q6, Q7, Q8, Q9, Q10, Q11, Q12: LNG03R031; TO-252-2
R23, R29, R38, R43, R48: 10R; R_1206_3216Metric_Pad1.42x1.75mm_HandSolder
U7, U8, U10, U11, U13: LM5106MM_NOPB; LM5106MM_slash_NOPB

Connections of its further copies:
/Motor1_Output_Power_Stage_B/MOTOR_OUT_PHASE_X: C19.2, D13.2 (A), D14.1 (K), Q3.3 (S), Q4.2 (D), U7.4 (HS); also elsewhere on the board
/Motor1_Output_Power_Stage_C/MOTOR_OUT_PHASE_X: C22.2, D18.2 (A), D19.1 (K), Q5.3 (S), Q6.2 (D), U8.4 (HS); also elsewhere on the board
/Motor2_Output_Power_Stage_A/MOTOR_OUT_PHASE_X: C24.2, D23.2 (A), D24.1 (K), Q7.3 (S), Q8.2 (D), U10.4 (HS); also elsewhere on the board
/Motor2_Output_Power_Stage_B/MOTOR_OUT_PHASE_X: C26.2, D28.2 (A), D29.1 (K), Q9.3 (S), Q10.2 (D), U11.4 (HS); also elsewhere on the board
/Motor2_Output_Power_Stage_C/MOTOR_OUT_PHASE_X: C28.2, D33.2 (A), D34.1 (K), Q11.3 (S), Q12.2 (D), U13.4 (HS); also elsewhere on the board
GND: C20.2, C23.2, C25.2, C27.2, C29.2, D14.2 (A), D19.2 (A), D24.2 (A), D29.2 (A), D34.2 (A), Q4.3 (S), Q6.3 (S), Q8.3 (S), Q10.3 (S), Q12.3 (S), U7.9 (VSS), U8.9 (VSS), U10.9 (VSS), U11.9 (VSS), U13.9 (VSS); also elsewhere on the board
MOTOR1_ENABLE: U7.7 (EN), U8.7 (EN); also elsewhere on the board
MOTOR1_PWM_B: U7.8 (IN); also elsewhere on the board
MOTOR1_PWM_C: U8.8 (IN); also elsewhere on the board
MOTOR1_V_IN: D13.1 (K), D18.1 (K), Q3.2 (D), Q5.2 (D); also elsewhere on the board
MOTOR2_ENABLE: U10.7 (EN), U11.7 (EN), U13.7 (EN); also elsewhere on the board
MOTOR2_PWM_A: U10.8 (IN); also elsewhere on the board
MOTOR2_PWM_B: U11.8 (IN); also elsewhere on the board
MOTOR2_PWM_C: U13.8 (IN); also elsewhere on the board
MOTOR2_V_IN: D23.1 (K), D28.1 (K), D33.1 (K), Q7.2 (D), Q9.2 (D), Q11.2 (D); also elsewhere on the board
unnamed: C19.1, D10.1 (K), U7.2 (HB)
unnamed: C22.1, D15.1 (K), U8.2 (HB)
unnamed: C24.1, D20.1 (K), U10.2 (HB)
unnamed: C26.1, D25.1 (K), U11.2 (HB)
unnamed: C28.1, D30.1 (K), U13.2 (HB)
unnamed 61: D11.1 (K); also elsewhere on the board
unnamed 62: D11.2 (A), Q3.1 (G); also elsewhere on the board
unnamed: D12.1 (K), R23.1
unnamed 64: D12.2 (A), Q4.1 (G); also elsewhere on the board
unnamed 65: D16.1 (K); also elsewhere on the board
unnamed 66: D16.2 (A), Q5.1 (G); also elsewhere on the board
unnamed: D17.1 (K), R29.1
unnamed 68: D17.2 (A), Q6.1 (G); also elsewhere on the board
unnamed 69: D21.1 (K); also elsewhere on the board
unnamed 70: D21.2 (A), Q7.1 (G); also elsewhere on the board
unnamed: D22.1 (K), R38.1
unnamed 72: D22.2 (A), Q8.1 (G); also elsewhere on the board
unnamed 73: D26.1 (K); also elsewhere on the board
unnamed 74: D26.2 (A), Q9.1 (G); also elsewhere on the board
unnamed: D27.1 (K), R43.1
unnamed 76: D27.2 (A), Q10.1 (G); also elsewhere on the board
unnamed 77: D31.1 (K); also elsewhere on the board
unnamed 78: D31.2 (A), Q11.1 (G); also elsewhere on the board
unnamed: D32.1 (K), R48.1
unnamed 80: D32.2 (A), Q12.1 (G); also elsewhere on the board
unnamed 84: U7.6 (RDT); also elsewhere on the board
unnamed 85: U7.3 (HO); also elsewhere on the board
unnamed 86: R23.2, U7.10 (LO); also elsewhere on the board
unnamed 87: U8.6 (RDT); also elsewhere on the board
unnamed 88: U8.3 (HO); also elsewhere on the board
unnamed 89: R29.2, U8.10 (LO); also elsewhere on the board
unnamed 90: U10.6 (RDT); also elsewhere on the board
unnamed 91: U10.3 (HO); also elsewhere on the board
unnamed 92: R38.2, U10.10 (LO); also elsewhere on the board
unnamed 93: U11.6 (RDT); also elsewhere on the board
unnamed 94: U11.3 (HO); also elsewhere on the board
unnamed 95: R43.2, U11.10 (LO); also elsewhere on the board
unnamed 96: U13.6 (RDT); also elsewhere on the board
unnamed 97: U13.3 (HO); also elsewhere on the board
unnamed 98: R48.2, U13.10 (LO); also elsewhere on the board
V_DRIVERS: C20.1, C23.1, C25.1, C27.1, C29.1, D10.2 (A), D15.2 (A), D20.2 (A), D25.2 (A), D30.2 (A), U7.1 (VDD), U8.1 (VDD), U10.1 (VDD), U11.1 (VDD), U13.1 (VDD); also elsewhere on the board

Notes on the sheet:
<- new cap tests showed this reduces noise cased by mosfet switching
With VDD=9V of Gate Driver Rmax_rise = 7ohm (1.3A) -> use 10ohm Rmax_fall = 5ohm (1.8A) -> 10 ohm for diode in parallel 10ohm -> 5ohm
Diode Candidates (fast switching): - UF4007
Gate Resistor calculations:

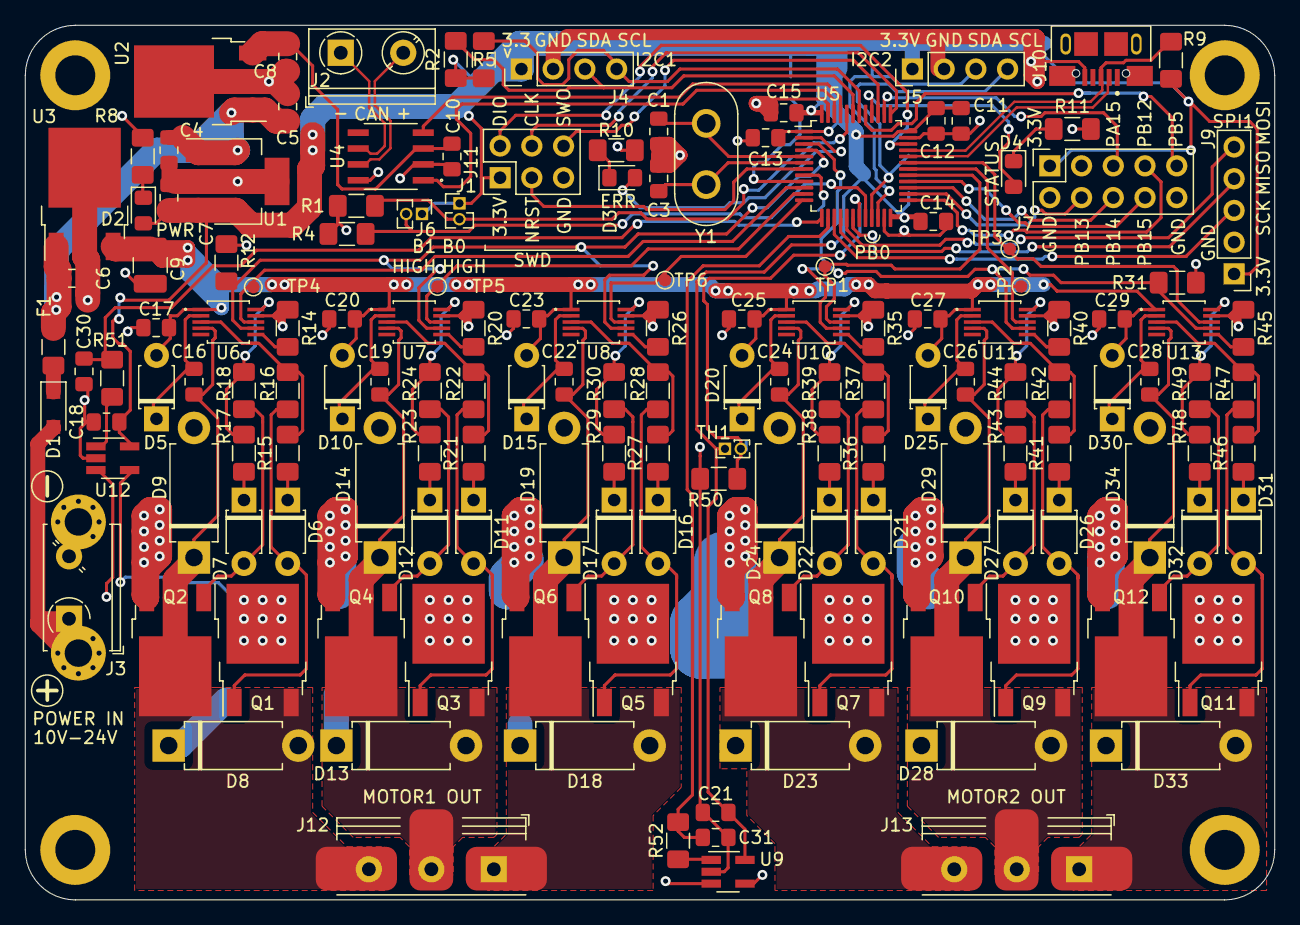
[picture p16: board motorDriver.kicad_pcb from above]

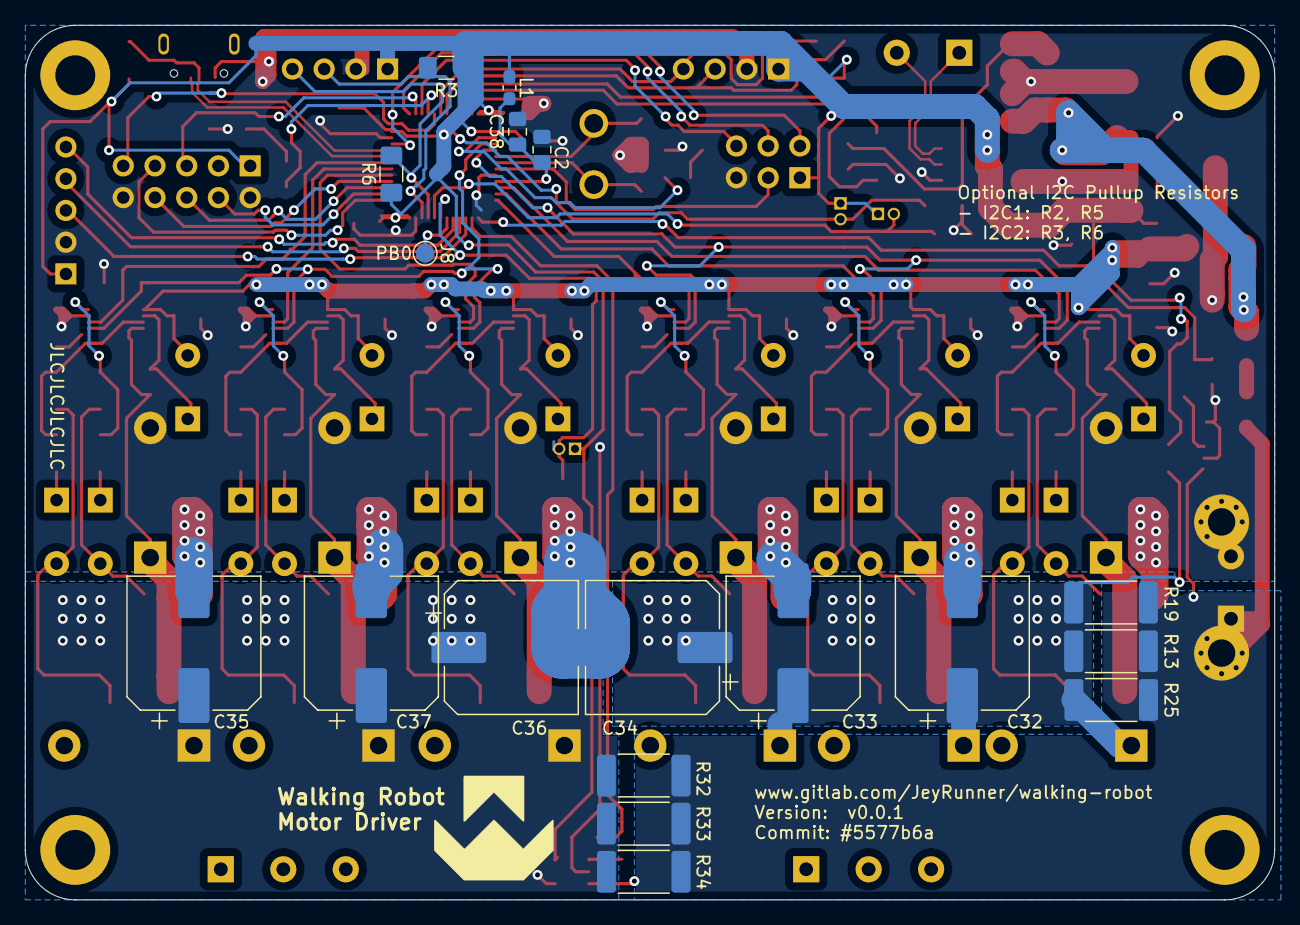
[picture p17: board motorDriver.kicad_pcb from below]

Board: 2 copper layers, 100.0 x 70.0 mm, 177 parts (19 on the bottom side), 110 nets.

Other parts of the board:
R20, R26, R35, R40, R45: 47R; R_1206_3216Metric_Pad1.42x1.75mm_HandSolder
R21, R27, R36, R41, R46: 5R; R_1206_3216Metric_Pad1.42x1.75mm_HandSolder
R22, R28, R37, R42, R47: 3.3R; R_1206_3216Metric_Pad1.42x1.75mm_HandSolder
R24, R30, R39, R44, R49: 22R; R_1206_3216Metric_Pad1.42x1.75mm_HandSolder
kibuzzard-642D7167: G***; kibuzzard-642D7167

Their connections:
GND: R20.2, R26.2, R35.2, R40.2, R45.2; also elsewhere on the board
unnamed 61: R21.1; also elsewhere on the board
unnamed 62: R22.1; also elsewhere on the board
unnamed 64: R24.1; also elsewhere on the board
unnamed 65: R27.1; also elsewhere on the board
unnamed 66: R28.1; also elsewhere on the board
unnamed 68: R30.1; also elsewhere on the board
unnamed 69: R36.1; also elsewhere on the board
unnamed 70: R37.1; also elsewhere on the board
unnamed 72: R39.1; also elsewhere on the board
unnamed 73: R41.1; also elsewhere on the board
unnamed 74: R42.1; also elsewhere on the board
unnamed 76: R44.1; also elsewhere on the board
unnamed 77: R46.1; also elsewhere on the board
unnamed 78: R47.1; also elsewhere on the board
unnamed 80: R49.1; also elsewhere on the board
unnamed 84: R20.1; also elsewhere on the board
unnamed 85: R21.2, R22.2; also elsewhere on the board
unnamed 86: R24.2; also elsewhere on the board
unnamed 87: R26.1; also elsewhere on the board
unnamed 88: R27.2, R28.2; also elsewhere on the board
unnamed 89: R30.2; also elsewhere on the board
unnamed 90: R35.1; also elsewhere on the board
unnamed 91: R36.2, R37.2; also elsewhere on the board
unnamed 92: R39.2; also elsewhere on the board
unnamed 93: R40.1; also elsewhere on the board
unnamed 94: R41.2, R42.2; also elsewhere on the board
unnamed 95: R44.2; also elsewhere on the board
unnamed 96: R45.1; also elsewhere on the board
unnamed 97: R46.2, R47.2; also elsewhere on the board
unnamed 98: R49.2; also elsewhere on the board

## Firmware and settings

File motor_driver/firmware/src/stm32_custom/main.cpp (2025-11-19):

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
/* Includes ------------------------------------------------------------------*/
#include "main.h"
#include "adc.h"
#include "can.h"
#include "dma.h"
#include "i2c.h"
#include "spi.h"
#include "tim.h"
#include "usb_device.h"
#include "gpio.h"

/* USER CODE BEGIN Includes */
#include "MotorDriver.hpp"
#include "motordriver/util/util.h"
//#include "can_stm32.h"
//#include "stm32_custom/testing.h"

/* USER CODE END Includes */


void SystemClock_Config(void);
/**
  * @brief  The application entry point.
  * @retval int
  */
int main(void)
{
  /* MCU Configuration--------------------------------------------------------*/

  /* Reset of all peripherals, Initializes the Flash interface and the Systick. */
  HAL_Init();

  /* Configure the system clock */
  SystemClock_Config();

  /* USER CODE BEGIN SysInit */

  MX_GPIO_Init();
  // rest USB
  // call before USB init and after MX_GPIO_Init()
  usbRest();

  /* USER CODE END SysInit */

  /* Initialize all configured peripherals */

  MX_DMA_Init();
  MX_TIM1_Init();
  MX_I2C1_Init();
  MX_I2C2_Init();
  MX_SPI1_Init();
  MX_TIM2_Init();
  MX_TIM3_Init();
  MX_SPI2_Init();
  MX_ADC1_Init();
  MX_USB_DEVICE_Init();
  MX_CAN_Init();
  /* USER CODE BEGIN 2 */

  /// @note: when can is used (MX_CAN_Init is called) the usb interface will not work anymore


  i2c_1 = &hi2c1;
  i2c_2 = &hi2c2;
  timer_htim1 = &htim1;

  // enable pwms
  /*
  HAL_TIM_PWM_Start(&htim1,TIM_CHANNEL_1);
  HAL_TIM_PWM_Start(&htim1,TIM_CHANNEL_2);
  HAL_TIM_PWM_Start(&htim1,TIM_CHANNEL_3);
  */

  //canSetup();
  setup();
  program();

  /* USER CODE END 2 */

  /* Infinite loop */
  /* USER CODE BEGIN WHILE */
  //canSetup();
  while (1)
  {
    /* USER CODE END WHILE */
    HAL_GPIO_TogglePin(LED_GREEN_GPIO_Port, LED_GREEN_Pin);
    HAL_Delay(1000);
    //printf("test \n");
    //CanCommunication::canSendPackageTypeWhenTxIsFree(CAN_PACKAGE_TYPE::SETUP_RESPONSE, 0);
    //canSendDataTest();
    // testWriteUsb();
    /* USER CODE BEGIN 3 */
  }
  /* USER CODE END 3 */
}

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


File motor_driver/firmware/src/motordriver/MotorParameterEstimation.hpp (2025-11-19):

#pragma once

#include "etl/delegate.h"
#include "config.h"
#include "motordriver/util/util.h"
#include "modulation/SpaceVectorModulation.h"
#include "Motor.hpp"

#include "util/EventFlag.h"


class MotorParameterEstimator {
  public:
    Motor &motor;

    /// will be set to true when parameter estimation is completed
    EventFlag estimationDone;


    /// gets called in shot intervalls during blocking execution of initEstimateMotorConfig(...)
    /// use this to e.g. check for events/exec code during this blocking execution;
    etl::optional<etl::delegate<void()>> estimationTickCallback;

    explicit MotorParameterEstimator(Motor &motor) : motor(motor) {}

    /**
     * Estimate motor parameters by slowly rotating the motor for a short time. This will temporarily enable the motor.
     * Call this function to init the motor parameters before any call to applyPhaseAngle(...).
     * @param encoder the initialized position encoder for this motor.
     * @param determineElectricalRotationsPerRevolution if this is true also the electricalRotationsPerRevolution will be measured.
     *                                                  if this is set to false motorConfig.electricalRotationsPerRevolution has to be set before calling this function
     */
    void initEstimateMotorConfig(Encoder &encoder, bool determineElectricalRotationsPerRevolution = true,  int motorThrottle = 120) {
      estimationDone.clear();
      motor.enableMotor(true);

      log("\n");
      log("record motor phase mapping ...");

      // find out positive encoder direction
      log("- find positive direction ...");
      // do 4 [electrical] rotation of the motor
      int checkElectricalInitialWarmupRotationNum = 2;
      int checkElectricalRotationNumber = 5;

      /*
      float elOffset_avg_num = 0;
      float elOffset_avg_sum = 0;
      */

      EncoderAngle angle_start(0);
      long last = 0;

      HAL_Delay(200);
      callTickCallback();
      printf("start \n");
      HAL_Delay(200);

      /// first find out motor direction and number of pole pairs
      for (int rotationIndex = 0;
           rotationIndex < (checkElectricalInitialWarmupRotationNum + checkElectricalRotationNumber); ++rotationIndex) {
        // do one electrical rotation
        for (int angleEl = 0; angleEl < MODULATION_DATA_FULLROTATION_VALUE; angleEl++) {
          motor.applyPhaseAngleSpaceVector(angleEl, motorThrottle);

          HAL_Delay(1);
          HAL_GPIO_TogglePin(LED_GREEN_GPIO_Port, LED_GREEN_Pin);
          EncoderAngle angle = encoder.update();
          //printf("%ld \n", angle.angle);

          /*
          float elOffset = fmod(angle*7 + elAngleNorm, PI_2);
          //printf("chartUpdate: %f, %f,   %f \n", angle, elAngleNorm, elOffset);
          printf("chartUpdate: %lu,   %f, %f\n", HAL_GetTick(), -angle, fmod(elAngleNorm, PI_2));
          elOffset_avg_num++;
          elOffset_avg_sum += elOffset;
          //printf("offset: %f, %f \n", angle, elAngleNorm);
          */
          callTickCallback();
        }

        long curAngle = encoder.getAngleAbsolute().angle;
        log("completed rotation [%d], encoder now at: %ld  (delta %ld)\n", rotationIndex, curAngle, abs(curAngle - last));
        last = curAngle;


        if (rotationIndex == (checkElectricalInitialWarmupRotationNum-1)) {
          HAL_Delay(200);
          angle_start = encoder.getAngleAbsolute();
          log("\nstart measuring...\n");
        }
      }

      EncoderAngle angle_end = encoder.update();

      // direction
      motor.motorConfig.motorDirection = (angle_end.angle > angle_start.angle)
                                    ? Motor::MOTOR_DIRECTION::POSITIVE : Motor::MOTOR_DIRECTION::INVERSE;

      // electricalRotationsPerRevolution
      long motorMovedAbsEncoder = abs(angle_end.angle - angle_start.angle);
      log("moved avg %f", (motorMovedAbsEncoder / (float) checkElectricalRotationNumber));
      float electricalRotationsPerRevolutionExact =
          Encoder::ENCODER_MAX_VALUE / (motorMovedAbsEncoder / (float) checkElectricalRotationNumber);
      if (determineElectricalRotationsPerRevolution) {
        motor.motorConfig.electricalRotationsPerRevolution = (int) std::round(electricalRotationsPerRevolutionExact);
      }
      //motorConfig.encoderRotationPerElectricalRotation = PI_2 / (float) motorConfig.electricalRotationsPerRevolution;

      initEstimateMotorConfig_encoderOffset(encoder, motorThrottle);
      HAL_Delay(50);
      callTickCallback();
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

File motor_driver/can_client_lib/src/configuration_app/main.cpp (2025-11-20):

#include <MotorDriverCanMaster.hpp>
#include <unistd.h>


#include <lyra/lyra.hpp>
using namespace lyra;



// args
string args_canInterface = "can0";
unsigned int args_clientId;
optional<float> args_gainP = nullopt;
optional<float> args_gainD = nullopt;
optional<float> args_velocityFilterTF = nullopt;


void parseArgs(int argc, const char **argv) {
  auto cli = lyra::cli();
  bool showHelp = false;
  cli.add_argument(help(showHelp));
  cli.add_argument(lyra::opt(args_canInterface, "can-interface" )["-i"]["--can-interface"]("The can interface to connect to"));
  cli.add_argument(lyra::opt(args_clientId, "client-id" )["--client-id"]("The can sot ID of the motordriver to connect to").required(true));
  cli.add_argument(lyra::opt(args_gainP, "Gain P")["-p"]["--set-gain-p"]("Set the proportional gain of the PD controller").optional());
  cli.add_argument(lyra::opt(args_gainD, "Gain D")["-d"]["--set-gain-d"]("Set the derivative gain of the PD controller").optional());
  cli.add_argument(lyra::opt(args_velocityFilterTF, "TF")["-f"]["--set-velocity-filter-tf"]("Set the time constant value of the velocity filter").optional());

  // parse args
  auto cli_result = cli.parse({argc, argv});

  // Check that the arguments where valid:
  if (!cli_result){
    std::cerr << "Error in command line: " << cli_result.message() << std::endl;
    exit(1);
  }

  if (showHelp){
    std::cout << endl << cli << std::endl;
    exit(0);
  }
}


int main(int argc, const char **argv) {
  parseArgs(argc, argv);

  MotorDriverCanMaster master(args_canInterface);
  if (!master.startCanInterface()) {
    exit(1);
  }
  cout << "connected to " << args_canInterface << "" << " can interface" << endl;
  master.canMaster.addAndConnectToClient(args_clientId);
  auto &client = master.canMaster.getClient(args_clientId);


  cout << "will connect to client " << endl;
  int i = 0;
  while (!client.isConnected()) {
    master.canMaster.processCanFrames();
    usleep(1000);
    i++;
    if (i>= 1000) {
      cout <<"Error: connecting to client timeout" << endl;
      exit(1);
    }
  }
  cout << "connected to client with id " << args_clientId << endl;


  if (args_gainP || args_gainD) {
    cout << "will set pd gains ..." << endl;
    cout << "Error -> Not implemented yet" << endl;
    exit(1);
    //bool ok = driverCanClient.sendSetPD(nullopt, nullopt, args_gainP, args_gainD);
    //cout << "set pd gains -> " << (ok ? "done" : "failed") << endl;
  }
  if (args_velocityFilterTF) {
    cout << "will set velocityFilterTF ..." << endl;
    client.protocol.objectTree.settings.velocity_filter.smoothingTf.write(args_velocityFilterTF.value()).sendValue();
    cout << "set velocityFilterTF -> done " << endl;
  }
}

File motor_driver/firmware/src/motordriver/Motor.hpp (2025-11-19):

#pragma once

#include "config.h"
#include "motordriver/util/util.h"
#include "modulation/SpaceVectorModulation.h"



class Motor {
  public:
    /// set these before init
    TIM_HandleTypeDef *pwmTimer = nullptr;
    GPIO_TypeDef *motorEnablePort = nullptr;
    uint16_t motorEnablePin = 0;

    bool motorEnabled = false;

    uint16_t lastAppliedThrottle = 0;


    enum class MOTOR_DIRECTION {
        POSITIVE = 0, // same direction as the encoder
        INVERSE = 1  // inverse direction as the encoder
    };

    /// set by initEstimateMotorConfig()
    struct MotorConfig {
        /// does MotorConfig contain valid values
        bool isValid = false;

        int encoderElectricalOffset = 0;
        int electricalRotationsPerRevolution = 0;
        MOTOR_DIRECTION motorDirection = MOTOR_DIRECTION::POSITIVE;
    } motorConfig;



    /**
     * Init will start the PWM timers required to produce output signals for the motor phases.
     */
    void init() {
      // enable pwm channels
      HAL_TIM_PWM_Start(pwmTimer, TIM_CHANNEL_1);
      HAL_TIM_PWM_Start(pwmTimer, TIM_CHANNEL_2);
      HAL_TIM_PWM_Start(pwmTimer, TIM_CHANNEL_3);
    }



  public:
    /**
     * Enable and disable the motor output.
     * @param enable when set to false all motor output are connected to GND, because MOSFET drivers are then disabled.
     */
    void enableMotor(bool enable) {
      this->motorEnabled = enable;
      HAL_GPIO_WritePin(motorEnablePort, motorEnablePin,
                        (this->motorEnabled ? GPIO_PIN_SET : GPIO_PIN_RESET)
                        );
    }





    /**
     * Apply motor a field via the space vector PWM method.
     * The field is given by an angle and amplitude (throttle)
     * @param angleElectrical the fields electrical angle (will be normalized within ths call)
     * @param throttle the field strength [0 ... 1000]
     */
    void applyPhaseAngleSpaceVector(long angleElectrical, int throttle) {
      lastAppliedThrottle = throttle;
      Vec3 phaseValues = getModulationValues<MODULATION_TYPE::SINUS>(angleElectrical);
      // scale by throttle
      // shift by half max value upwards -> 50% duty circle is virtual Zero
      phaseValues.a = (phaseValues.a * throttle) / 1000 + MODULATION_DATA_MAX_VALUE;
      phaseValues.b = (phaseValues.b * throttle) / 1000 + MODULATION_DATA_MAX_VALUE;
      phaseValues.c = (phaseValues.c * throttle) / 1000 + MODULATION_DATA_MAX_VALUE;

      setOutput(phaseValues.a, phaseValues.b, phaseValues.c);
    }




    static constexpr int ANGLE_MAX = 1000;
    static constexpr int ANGLE_1_3_ROTATION = (int)((float)ANGLE_MAX * (1.0/3));
    static constexpr int ANGLE_1_6_ROTATION = (int)((float)ANGLE_MAX * (1.0/6));

/*
    void applyPhaseAngle2PI(float angle, float throttle = 1.0) {
      float f = angle / PI_2;
      int applInt = (int) (fmod(f, 1.0) * 1000);
      applInt = (applInt < 0) ? (1000 + applInt) : applInt;
      applyPhaseAngle(applInt, throttle);
    }


    void applyPhaseAngle(int angle, float throttle = 1.0) {
      if (angle < 0) {
        printf("motorPhase is negative [skip]: %d \n", angle);
        return;
      }

      int phaseA = 0;
      int phaseB = 0;
      int phaseC = 0;

      int mainSector = (int)((float)angle / ((float)ANGLE_MAX * (1.0/3)));  // 0,1,2
      int subSector = (int)((float)(angle - mainSector*((1.0/3) * ANGLE_MAX)) / ((float)ANGLE_MAX * (1.0/6)));   // 0,1

      int angleToNextMainSector = angle - ((int) mainSector*ANGLE_1_3_ROTATION);
      angleToNextMainSector = (subSector == 0) ? angleToNextMainSector : (ANGLE_1_3_ROTATION - angleToNextMainSector);

      int angleToNextMainSector_asPhaseValue = (int)(((float)angleToNextMainSector / (float)ANGLE_1_6_ROTATION) * (float)PHASE_MAX_VALUE);


      //printf("chartUpdate: %lu, %f, %d, %f \n", HAL_GetTick(), angle/1000.0, mainSector, angleToNextMainSector/1000.0);

      switch (mainSector) {
        case 0: {
          phaseC = 0;
          if (subSector == 0) {
            phaseA = PHASE_MAX_VALUE;
            phaseB = angleToNextMainSector_asPhaseValue;
          }
          else {
            phaseA = angleToNextMainSector_asPhaseValue;
            phaseB = PHASE_MAX_VALUE;
          }
        } break;

        case 1: {
          phaseA = 0;
          if (subSector == 0) {
            phaseB = PHASE_MAX_VALUE;
            phaseC = angleToNextMainSector_asPhaseValue;
          }
          else {
            phaseB = angleToNextMainSector_asPhaseValue;
            phaseC = PHASE_MAX_VALUE;
          }
        } break;

        case 2: {
          phaseB = 0;
          if (subSector == 0) {
            phaseC = PHASE_MAX_VALUE;
            phaseA = angleToNextMainSector_asPhaseValue;
          }
          else {
            phaseA = PHASE_MAX_VALUE;
            phaseC = angleToNextMainSector_asPhaseValue;
          }
        } break;
      }

      phaseA = (int) ((float)phaseA * THROTTLE * throttle);
      phaseB = (int) ((float)phaseB * THROTTLE * throttle);
      phaseC = (int) ((float)phaseC * THROTTLE * throttle);


      // min timer value is 100
      // otherwise no effect on output due to mosfet driver deadtime
      // constexpr int PHASE_MIN_VALUE = 25;
      // phaseA = (phaseA < PHASE_MIN_VALUE && phaseA > 0) ? PHASE_MIN_VALUE : phaseA;
      // phaseB = (phaseB < PHASE_MIN_VALUE && phaseB > 0) ? PHASE_MIN_VALUE : phaseB;
      // phaseC = (phaseC < PHASE_MIN_VALUE && phaseC > 0) ? PHASE_MIN_VALUE : phaseC;

      // printf("chartUpdate: %lu, %d, %d, %d \n", HAL_GetTick(), phaseA, phaseB, phaseC);
      setOutput(phaseA, phaseB, phaseC);
    }
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

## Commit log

2025-11-19 motor_driver firmware
    [motorControllerCanProtocol.def.yaml, motorControllerCanProtocol.spec.yaml, stm32F103_Debug_self_start.cfg]
2025-11-19 motor_driver hardware
    [Motor_Output_Power_Stage.kicad_sch, Motor_Output_Power_Stage.sch, Parts.ods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]
2025-11-20 added gearbox cad imgs
2025-11-20 cleanup kicad libs

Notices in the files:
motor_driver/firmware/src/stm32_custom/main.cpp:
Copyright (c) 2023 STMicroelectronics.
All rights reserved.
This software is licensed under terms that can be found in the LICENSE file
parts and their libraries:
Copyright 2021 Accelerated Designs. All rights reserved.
